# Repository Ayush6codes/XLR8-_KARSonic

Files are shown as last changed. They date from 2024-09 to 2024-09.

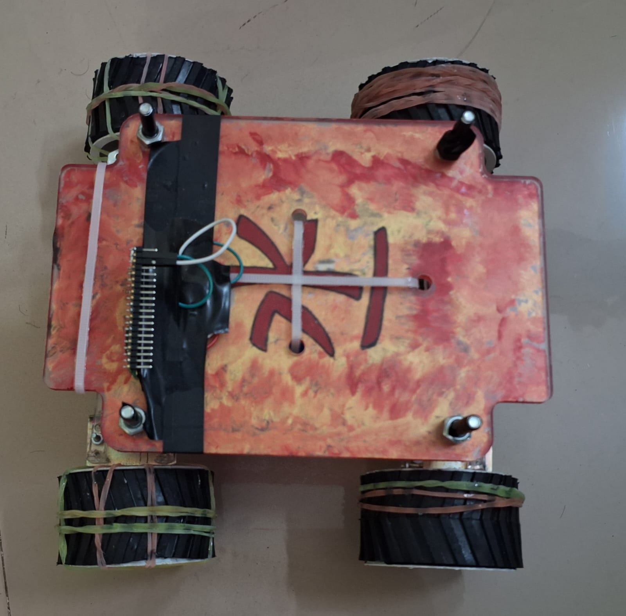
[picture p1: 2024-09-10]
Top.jpg

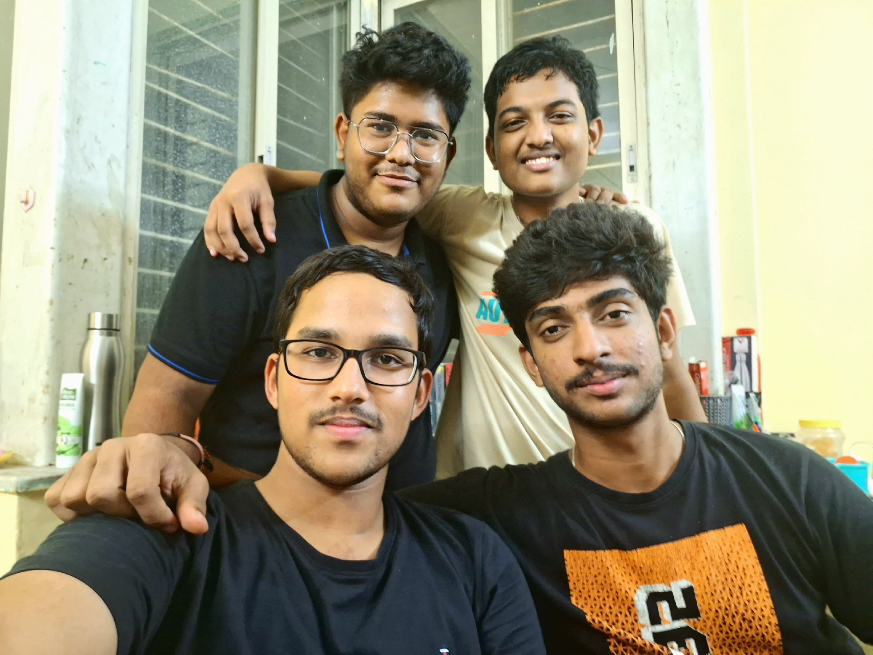
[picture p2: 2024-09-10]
KARSonic_Team.jpg

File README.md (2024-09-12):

# XLR8_KARSonic
Our team KARSonic's XLR8 Journey was very wonderful. We started working on our designs and strategies from the first day of the registrations itself. Then our mentor told us about a team that had included suspensions in their bot for last year's XLR8. We also thought of making a suspension system and worked on it for almost a week, trying different mechanisms, trying to stabilize the whole system, and effectively controlling the bot. Unfortunately, we couldn't make an effective suspension system before the final run, so we have kept that idea for later ;). Also, at first, we thought of using 300 rpm motors, but at 5:30 am on the day of the first run (and after pulling an all-nighter) we found that our bot couldn't go up an incline. So, we woke up at 8:30 am and ran to the stationery shop to buy 200 rpm motors. Our final model was completed at 9:30 am. Sadly, our bot couldn't run on the slopes of the main obstacle course and we had to skip many obstacles. We completed the first run in around 12 mins. We were utterly disappointed but not discouraged, we decided to give our best in the 2nd try. Then, we changed our wheels to 7X4 (we had used 10X4 in the first run), massively cut the weight of the bot, and lowered its height. We tested various codes on the day of the 2nd run and the final one was tested around 20 mins before the run, which helped turn in the slopes and gave us a massive time advantage. We completed the 2nd run in 4 mins 33s skipping only 1 obstacle. We learned more in that one day than in the one week we had been working on the bot.<br/>
Overall, it was a very nice experience, learning Mechanical, Electrical, and Coding aspects to a great depth and making a very innovative thing on our own.

# What makes our bot different
Our bot has a special feature we coded in the Raspberry Pi Pico W. First, it should be noted that we have used the differential drive. <br/>The bot can take two types of turns: <br/>1) Having some turn radius and moving while turning (basically like an Axle Drive) and 
<br/>2) Having 0 turn radius. 
<br/> We named the 1st as - "Small Turn" and the 2nd as - "Large Turn". The trigger for both is effortless. For example, if the controller is tilted right up to an angle of 70 degrees, then it will take a small right turn, while if it is tilted further than 70 degrees (up to 90) then it will take a large right turn. Same for the left. We also adjusted speeds and trigger angle (so that a small accidental tilt won't result in taking turns).
<br/><br/>
So what's the use of both types of turns ?
<br/><br/>
While taking turns on a slope, we noticed that the 2nd method of turning resulted in slipping of the bot. This was because 2 wheels moved in the reverse direction in this turning, and this caused them to slip and fall. Thus we developed the 1st method of turning, in which all the wheels move forward, but 2 of them slower (almost zero speed) than the others. Because of this method, the bot didn't slip while turning on slopes. Also, it resulted in faster turns at a few places which provided a time advantage in the competition. 
<br/><br/> We have shared the video of our innovative turn mechanism. <br/>NOTE: We have shared the model of our RC Car with the suspension system we were gonna (and are gonna) make. But the model for the run didn't have springs, just the bolts.

PS: The code was tested just 20-30 mins before our final run :)

# Help from our Mentor

Our mentors (Aditya Anmol and Abhinav Bijlani) helped us a lot. They cleared all our doubts regarding the controller, circuits, etc. We were also suggested and encouraged us in trying a suspension mechanism for our bot by Aditya. They helped us troubleshoot issues regarding our bot.

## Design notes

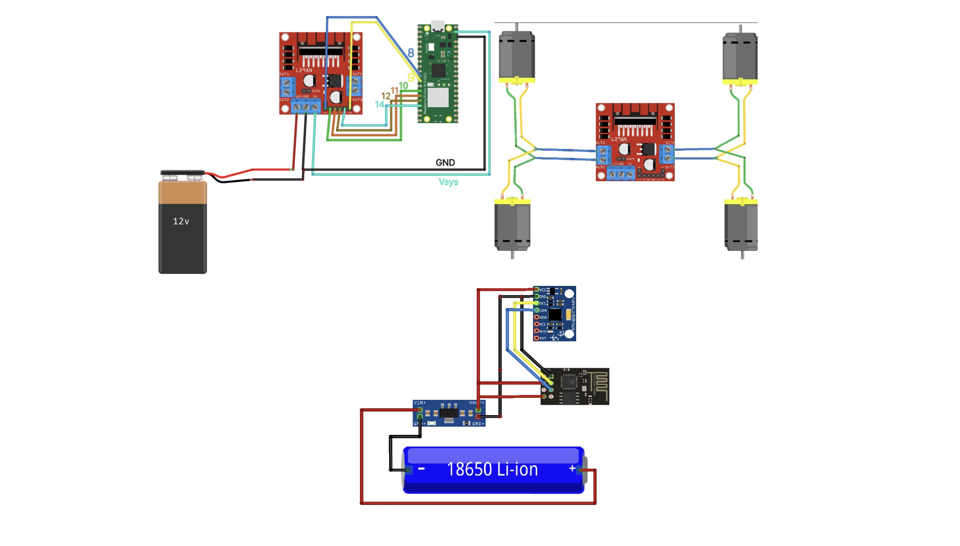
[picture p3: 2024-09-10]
Circuit Diagrams.jpg

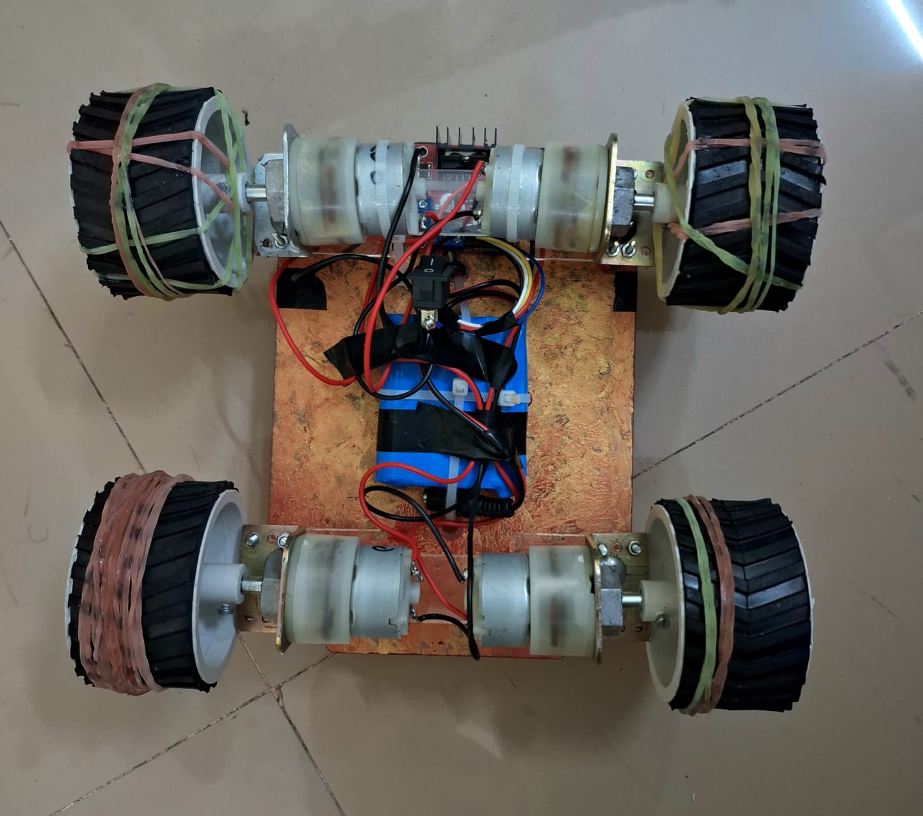
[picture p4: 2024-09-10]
Bottom.jpg

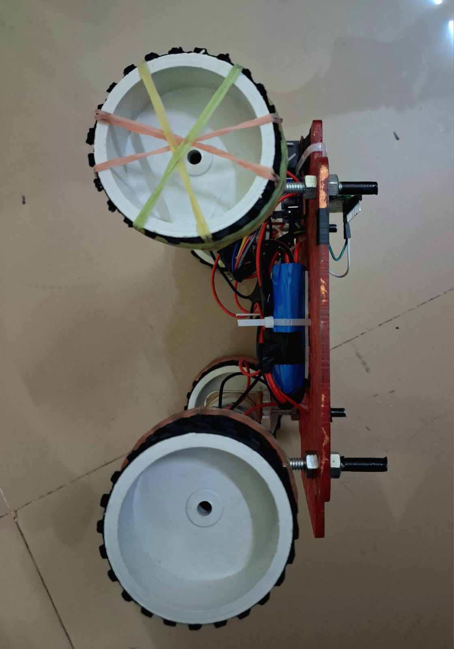
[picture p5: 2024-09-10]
Side.jpg

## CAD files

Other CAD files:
7x4 model V4.f3d

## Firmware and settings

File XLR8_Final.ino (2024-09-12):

#include <WiFi.h>
#include <typeinfo>
#include <string.h>
#include <stdio.h>

// SSID and password for the access point
const char* ssid = "KARSonic"; // Team name as the SSID 
const char* password = "Bando@69"; // Password

// Define a structure to hold IMU (Inertial Measurement Unit) data
typedef struct {
  float gx, gy, gz;
} IMUData;

IMUData myMessage; // Create a variable to store received IMU data
int cmd = 0;       // Initialize motor control command variable
int spd = 0;       // Initialize motor speed variable

// Function to update motor control based on received IMU data
void updateMotorControl() {
  float gx = myMessage.gx;
  float gy = myMessage.gy;
  float gz = myMessage.gz;

  // Motor control logic based on IMU data
  if ((gz != 0) && (gx != 0) && (abs(gy) < 2)) {
    spd = constrain(abs(map((atan2(gx, gz) * 180 / PI), 0, 90, 0, 255)), 0, 255);
    cmd = (gx > 0) ? 1 : 2; // Forward or backward
  } else if (((gz != 0) && (gy != 0) && (abs(gx) < 2)) && (atan2(gy, gz) * 180 / PI < 70)) {
    spd = constrain(abs(map((atan2(gy, gz) * 180 / PI), 0, 70, 200, 0)), 0, 200); //For small angle turns
    cmd = (gy > 0) ? 3 : 4; // For small angle Right or left
  } else if (((gz != 0) && (gy != 0) && (abs(gx) < 2)) && (atan2(gy, gz) * 180 / PI > 70)) {
    spd = constrain(abs(map((atan2(gy, gz) * 180 / PI), 70, 90, 0, 255)), 0, 255); //For large angle turns
    cmd = (gy > 0) ? 5 : 6; // For large angle Right or left
  } else {
    cmd = 0; // Stop
    spd = 0;
  }

  // Adjust motor speed thresholds
  if (((gz != 0) && (gx != 0) && (abs(gy) < 2)) && (spd > 60 && spd < 150) && (((gz != 0) && (gy != 0) && (abs(gx) < 2)) && (atan2(gy, gz) * 180 / PI > 70)))  {
    spd = 150;
  }
  if (((gz != 0) && (gx != 0) && (abs(gy) < 2)) && (spd > 150 && spd < 255) && (((gz != 0) && (gy != 0) && (abs(gx) < 2)) && (atan2(gy, gz) * 180 / PI > 70))) {
    spd = 255;
  }

  // Display motor control information
  Serial.print("cmd: ");
  Serial.print(cmd);   // Display motor command
  Serial.print(", speed: ");
  Serial.println(spd); // Display motor speed
}

// Pin assignments for motor control
const int ENA = 8;
const int ENB = 9;

const int IN1 = 10;
const int IN2 = 11;
const int IN3 = 12;
const int IN4 = 13;

// Create a WiFiServer object for the TCP server
WiFiServer server(80);

void setup() {
  // Start Serial for debugging
  Serial.begin(115200);
    // Configure motor control pins as outputs
  pinMode(LED_BUILTIN, OUTPUT);
  pinMode(ENA, OUTPUT);
  pinMode(IN1, OUTPUT);
  pinMode(IN2, OUTPUT);
  pinMode(ENB, OUTPUT);
  pinMode(IN3, OUTPUT);
  pinMode(IN4, OUTPUT);

  // Set up the access point
  Serial.println("Setting up WiFi AP...");
  WiFi.softAP(ssid, password);
  
  IPAddress IP = WiFi.softAPIP();
  Serial.print("AP IP address: ");
  Serial.println(IP);
  
  // Start the server
  server.begin();

  WiFiClient client = server.available();
  if (client) {
    Serial.println("Client is connected");
  }

}

void applyMotorControl() {
  float gx = myMessage.gx;
  float gy = myMessage.gy;
  float gz = myMessage.gz;
  switch (cmd) {
    case 1:  // Forward
      digitalWrite(IN1, LOW);
      digitalWrite(IN2, HIGH);
      digitalWrite(IN3, LOW);
      digitalWrite(IN4, HIGH);
      analogWrite(ENA, spd);
      analogWrite(ENB, spd);
      break;
    case 2:  // Backward
      digitalWrite(IN1, HIGH);
      digitalWrite(IN2, LOW);
      digitalWrite(IN3, HIGH);
      digitalWrite(IN4, LOW);
      analogWrite(ENA, spd);
      analogWrite(ENB, spd);
      break;
    case 3:  // Small Angle Right
      if (((gz != 0) && (gy != 0) && (abs(gx) < 2)) && (atan2(gy, gz) * 180 / PI > 30)) {
      digitalWrite(IN1, HIGH); 
      digitalWrite(IN2, LOW); 
      digitalWrite(IN3, HIGH);
      digitalWrite(IN4, LOW); 
      analogWrite(ENA, 255);
      analogWrite(ENB, 30);
      }
      break;
    case 4:  // Small Angle Left
      digitalWrite(IN1, HIGH);
      digitalWrite(IN2, LOW);
      digitalWrite(IN3, HIGH);
      digitalWrite(IN4, LOW);
      analogWrite(ENA, 30);
      analogWrite(ENB, 255);
      break;
    case 5:  // Large Angle Right
      digitalWrite(IN1, HIGH);
      digitalWrite(IN2, LOW);
      digitalWrite(IN3, LOW);
      digitalWrite(IN4, HIGH);
      analogWrite(ENA, 230);
      analogWrite(ENB, 230);
      break;
    case 6:  // Large Angle Left
      digitalWrite(IN1, LOW);
      digitalWrite(IN2, HIGH);
      digitalWrite(IN3, HIGH);
      digitalWrite(IN4, LOW);
      analogWrite(ENA, 230);
      analogWrite(ENB, 230);
      break;
    default:  // Stop
      digitalWrite(IN1, LOW); 
      digitalWrite(IN2, LOW); 
      digitalWrite(IN3, LOW); 
      digitalWrite(IN4, LOW); 
      spd = 0;
      analogWrite(ENA, spd);
      analogWrite(ENB, spd);
      break;
  }
}

void loop() {
  // Check if a client has connected
  WiFiClient client = server.available();
  //if (client) {
    //while (client.connected()) {
      if (client.available()) {
        digitalWrite(LED_BUILTIN, HIGH);
        String request = client.readStringUntil('\r');
        Serial.print("Received data: ");
        //Serial.println(request);
        char chararr[50];
        request.toCharArray(chararr, sizeof(chararr));

        Serial.println(chararr);
        char *res;
        float arr[3];
        int i = 0;

        res = strtok(chararr , " ");
        while(res != NULL){
          Serial.println(res);
          String strr = String(res);
          float val = strr.toFloat();
          Serial.println(val);
          res = strtok(NULL, " ");
          arr[i]= val;
          i++;
        }
        myMessage.gx = arr[0];
        myMessage.gy = arr[1];
        myMessage.gz = arr[2];
        updateMotorControl();
        applyMotorControl();
        digitalWrite(LED_BUILTIN, LOW);}
      digitalWrite(LED_BUILTIN, LOW);
   // Continuously update and apply motor control
  delay(100); // Delay to control loop speed
}
